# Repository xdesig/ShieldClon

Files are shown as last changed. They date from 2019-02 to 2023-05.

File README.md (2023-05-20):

# ShieldClon V 0.00 and 0.01 

## initial versions.

SlieldClon is a board designed, specifically for mClon. It allows secure connections to manipulate the robot. It has the basic components for its operation, as well as access to all free connections to be able to add new elements. The robot with ShieldClon feeds through a 18650 Li-ion battery 3.7V, which you can recharge through the board.
This plate can be complicated to weld by students that do not have much experience, since it has many components and pins very together, but it is a good challenge to learn.
From the mClon team, we consider it important that students understand the robot's internal functioning, who knows their components and what their function is, so we recommend starting from 4th of ESO not to give the plate already welded, unless previously practiced with protoShield. However, shieldClon can be a good option for work with younger students, always inviting them to connect the sensors and actresses on the shield pins themselves.
Is valid to be able to carry out many STEM projects based on Arduino

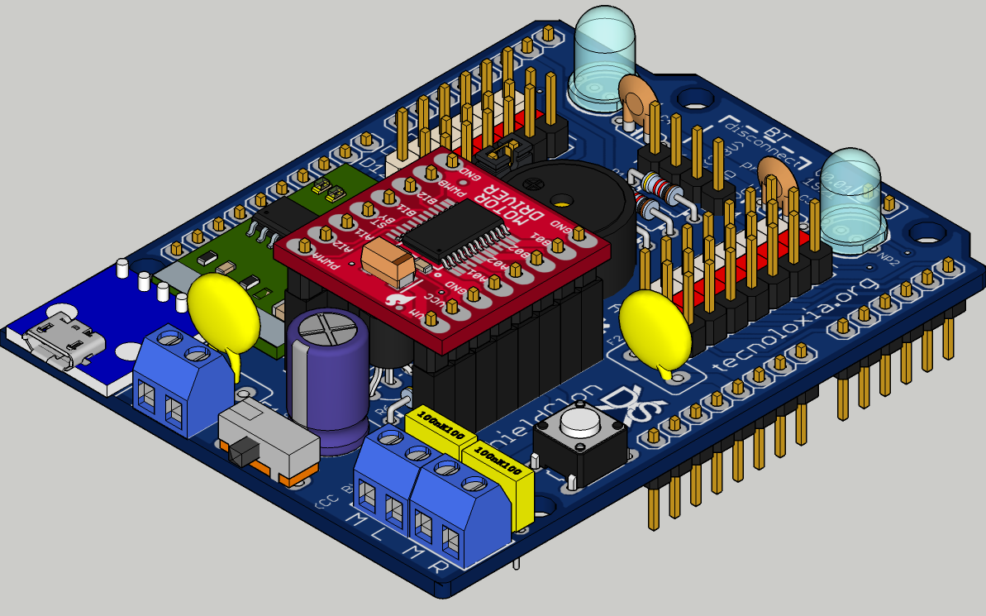
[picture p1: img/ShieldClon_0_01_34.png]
RENDER


### [Assembly manual][Man]
#### Deseñado en Estrimia con agarimo.

## Author and license
* Author: [XDeSIG][TWI01]
* License:
  CERN Open Hardware Licence Version 2 - Weakly Reciprocal"CERN-OHL-W"
  Doc. Attribution-ShareAlike 4.0 International "CCBY-SA4.0"
 

## More info:
[tecnoloxia.org]
## To buy boards

Developer don't produce boards to sell. Under [_provider_][provider]
directory there are instructions to order yourself.

<!-- links -->
[tecnoloxia.org]: https://tecnoloxia.org/mclon/que-e-mclon/
[CCBY-SA4.0]: http://creativecommons.org/licenses/by-sa/4.0/
[TWI01]: https://twitter.com/xdesig
[RENDER]: https://github.com/xdesig/ShieldClon/blob/master/img/ShieldClon_0_01_34.png
[provider]: https://www.pcbway.com/project/shareproject/W50475ASJ144_NanoClon_001_gerber_f511f448.html
[Man]: https://github.com/xdesig/ShieldClon/blob/master/ShieldClon_0_00/Montaxe_ShielClon.pdf

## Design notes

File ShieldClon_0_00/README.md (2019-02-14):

# ShieldClon V 0.00

## initial version.
Accessible connectors for basic function of MC LON. 
charge and discharge control for 3.7v batteries. 
Step-up voltage to 5V
Support for control of two engines in H bridge TB6612FNG.
Connection for two neopixel WS2812B through hole technology.
more info [tecnoloxia.org]
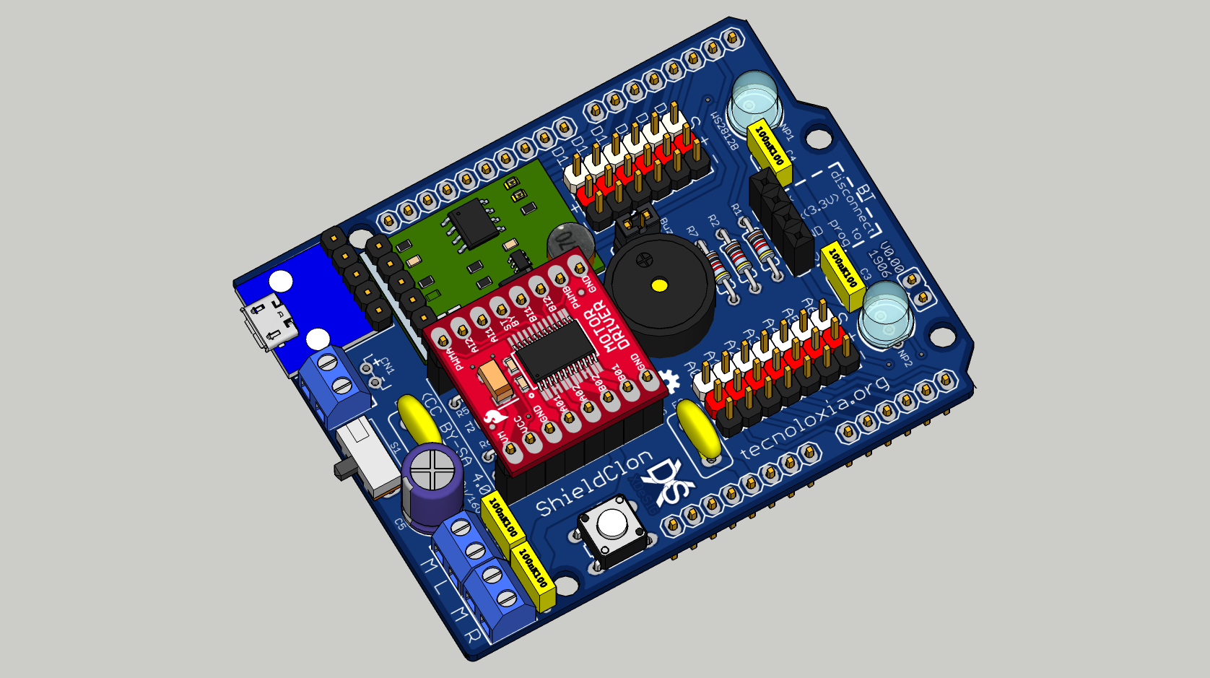
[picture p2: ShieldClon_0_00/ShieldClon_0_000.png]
Render ShieldClon 0.00


## Author and license
* Author: [XDeSIG][TWI01]
* License: [Attribution-ShareAlike 4.0 International] [CCBY-SA4.0]

<!-- links -->
[tecnoloxia.org]: https://tecnoloxia.org/mclon/que-e-mclon/
[CCBY-SA4.0]: http://creativecommons.org/licenses/by-sa/4.0/
[TWI01]: https://twitter.com/xdesig
[RENDER]: ShieldClon_0_000.png

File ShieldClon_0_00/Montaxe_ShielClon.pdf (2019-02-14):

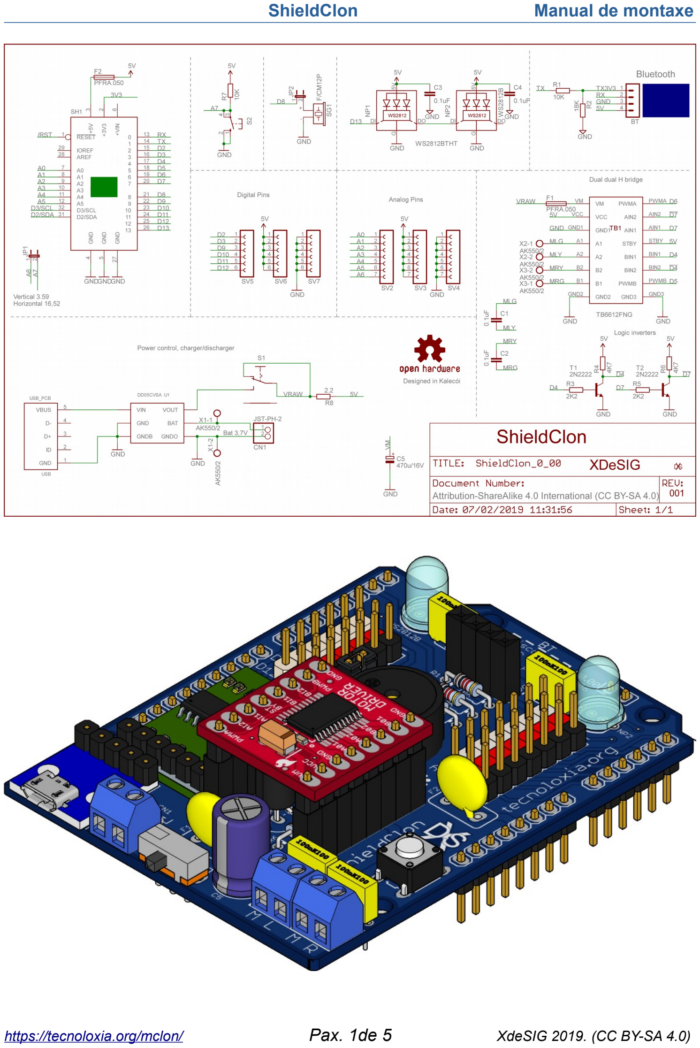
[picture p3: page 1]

ShieldClon | Manual de montaxe
https://tecnoloxia.org/mclon/ | Pax. 1de 5 | XdeSIG 2019. (CC BY-SA 4.0)

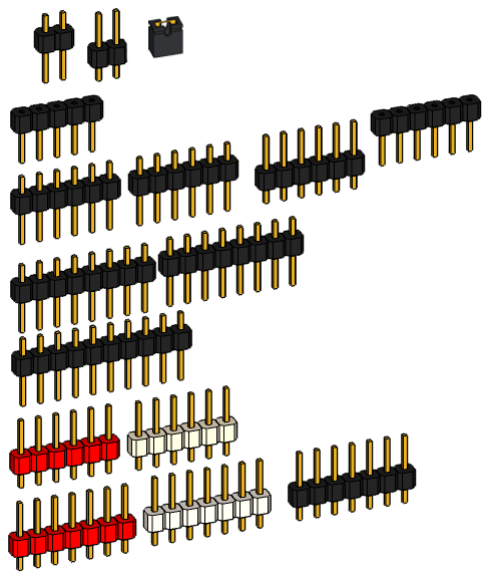
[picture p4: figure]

- Inventario de compoñentes.
- Tiras de postes
- 2 x 2 x 2,54mm + ponte
- 1 x 5 x 2,54mm
- 4 x 6 x 2,54mm
- 2 x 8 x 2,54mm
- 1 x 10 x 2,54mm
- 1 x 6 x 2,54mm Vermella
- 1 x 6 x 2,54mm Branca
- 1 x 7 x 2,54mm Vermella
- 1 x 7 x 2,54mm Branca
- 1 x 7 x 2,54mm Negra

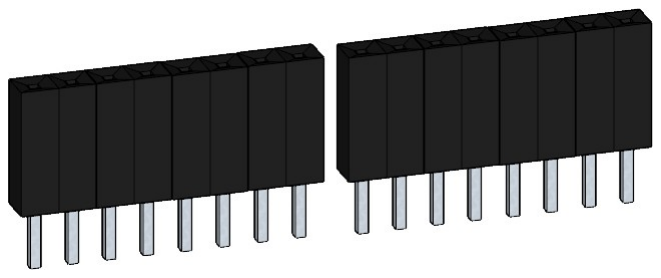
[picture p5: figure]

- Tiras Femia
- 1 x 4 x 2,54mm
- 2 x 8 x 2,54mm
- Bloques terminais
- 3 x 2 x 3,5mm
- Interruptor SK-12D07 e pulsador 6*6 6mm
- Resistencias:
- 2,2W, 18KW, 2 x 2K2W, 2 x 4K7W, 2 x 10KW.
- Condensadores:
- 4 x 100nF/≥16V, 470µF/≥16V
- Fusibles:
- 2 x Polyfuse 0,5mA
◦
- 2x LEDes NeoPixel WS2812B 5mm

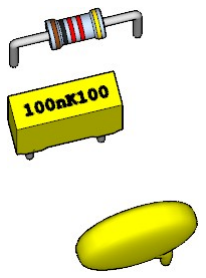
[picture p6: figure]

https://tecnoloxia.org/mclon/ | Pax. 2de 5 | XdeSIG 2019. (CC BY-SA 4.0)

- Módulos:
- Micro USB pcb
- Cargador/Booster
- Ponte “H” Dual

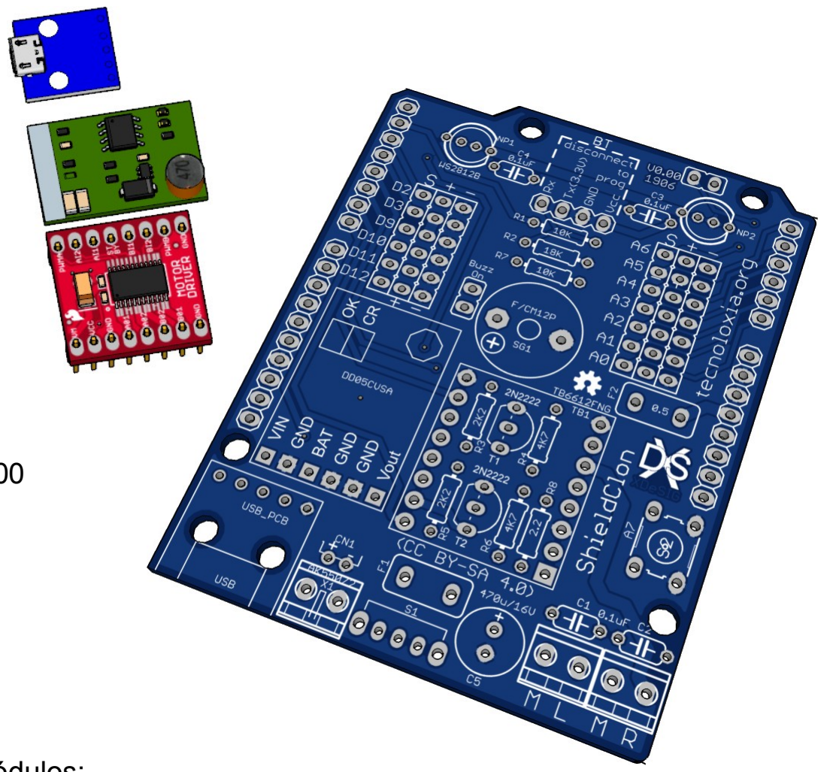
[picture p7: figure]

- PCB ShielClon V0,00
- Preparación dos módulos:
- Na placa micro USB tes que preparar unha tira de pins e baixalos de tal forma que queden cara abaixo, sóldao no modulo pola parte inferior,quedando como
na imaxe.

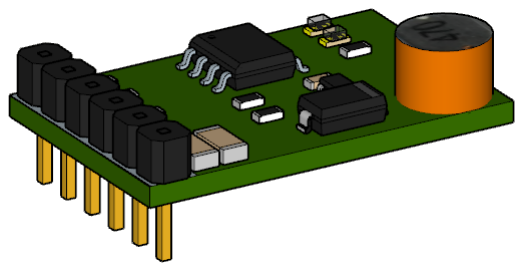
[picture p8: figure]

- No Cargador/Booster DD05CVSA fai o mesmo que na placa USB.
- A ponte “H” Dual TB6612FNG, xa
vén cos seus pines. Colócalos na parte inferior, procurando que queden o máis perpendiculares posible, sóldaos pola parte superior. Podes axudarte dunha protoboard
para pinchar os pins para que
queden perpendiculares (coidado ca

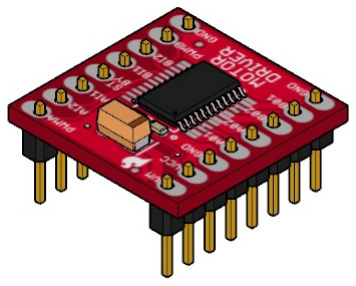
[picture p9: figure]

temperatura que protoboard non aguanta moito).

https://tecnoloxia.org/mclon/ | Pax. 3de 5 | XdeSIG 2019. (CC BY-SA 4.0)

- Na montaxe da placa, comeza polos compoñentes de baixo perfil, as resistencias. A placa ven serigrafiada cos

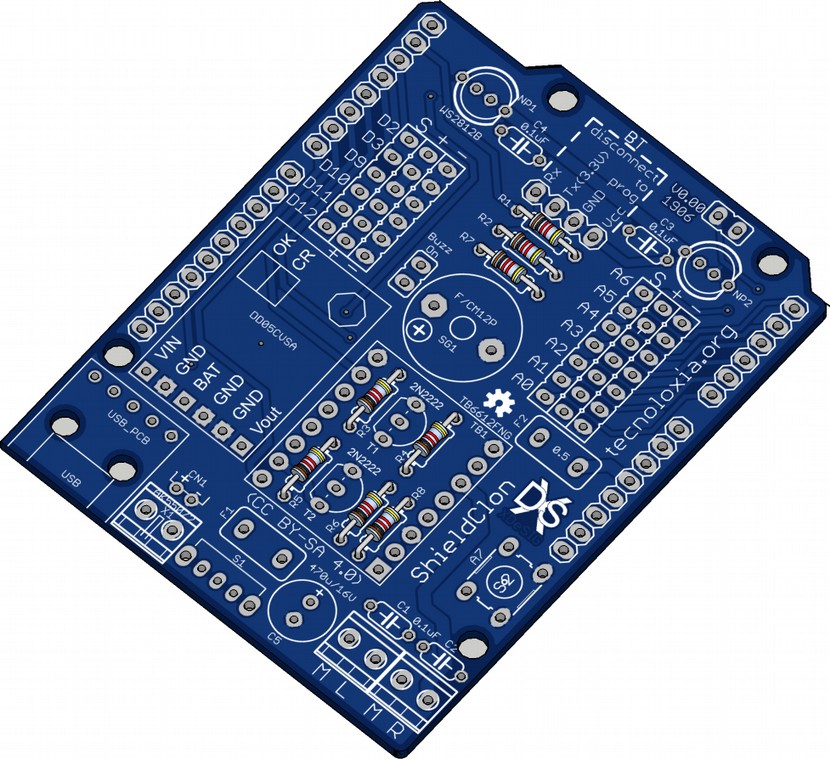
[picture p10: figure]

valores dos compoñentes. Vai soldando unha a
unha as resistencias, orientadas de tal forma
que sexan fáciles de ler, deixando a banda de tolerancia na dereita e vai cortando o sobrante das patas cada vez que soldes unha resistencia.
- Pasa a soldar os módulos que preparaches antes o modulo cargador/booster, e o adaptador USB ( podemos amarralo cunha brida que pasará polos buratos)

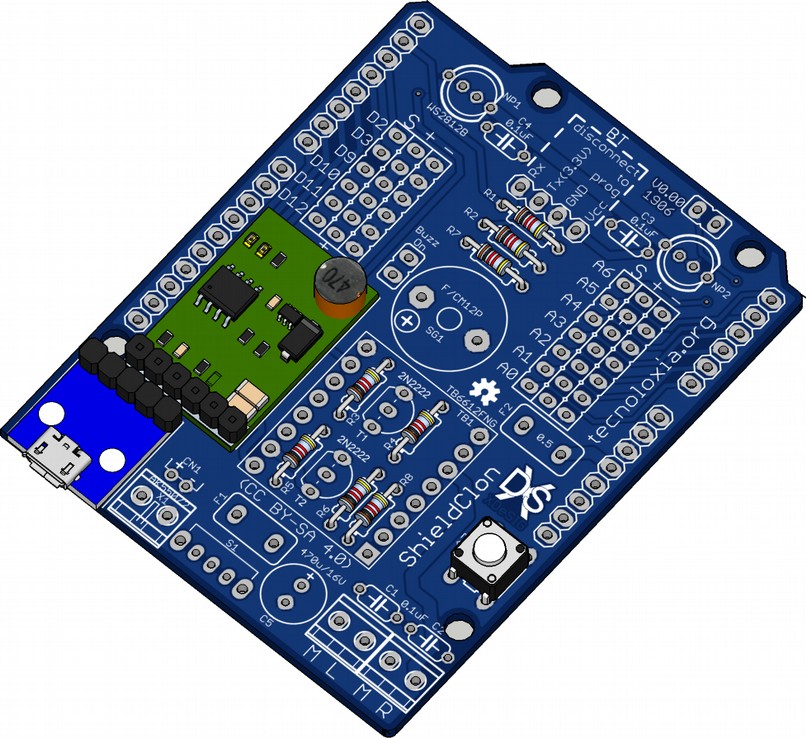
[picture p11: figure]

- Agora solda o interruptor, os conectores para os motores e alimentación.
Opcionalmente, se tes unha batería co conector JST-PH-2, podes soldar o conector macho nos Buratos CN1,
- Seguidamente soldamos os condensadores, os polyfuses e os transistores. Con estes últimos ten coidado de inserilos como se indica na serigrafía. Tamén ten coidado ao soldalos, pois só aguantan 300ºC durante 10 segundos.
- (Consello: solda unha pata de un transistor, e mentas soldas a do outro este se arrefria un pouco.)

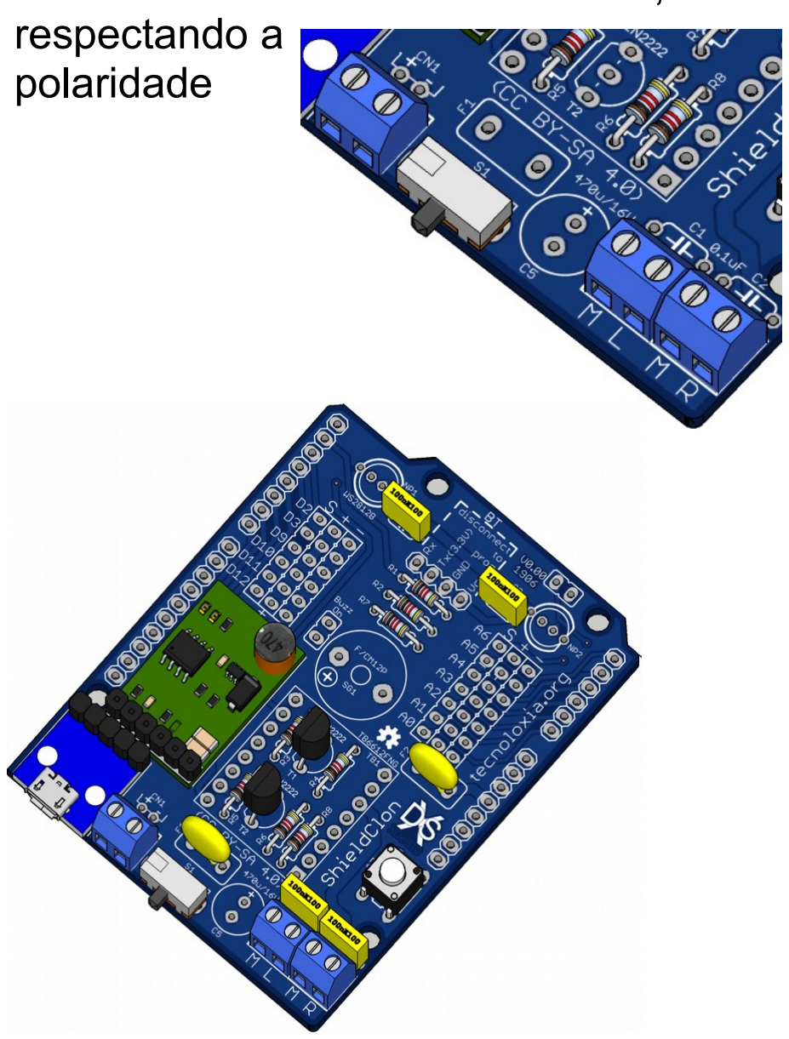
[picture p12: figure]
respectando a polaridade

https://tecnoloxia.org/mclon/ | Pax. 4de 5 | XdeSIG 2019. (CC BY-SA 4.0)

(ollo as cores das resistencias na imaxe non son correctas ) ☹

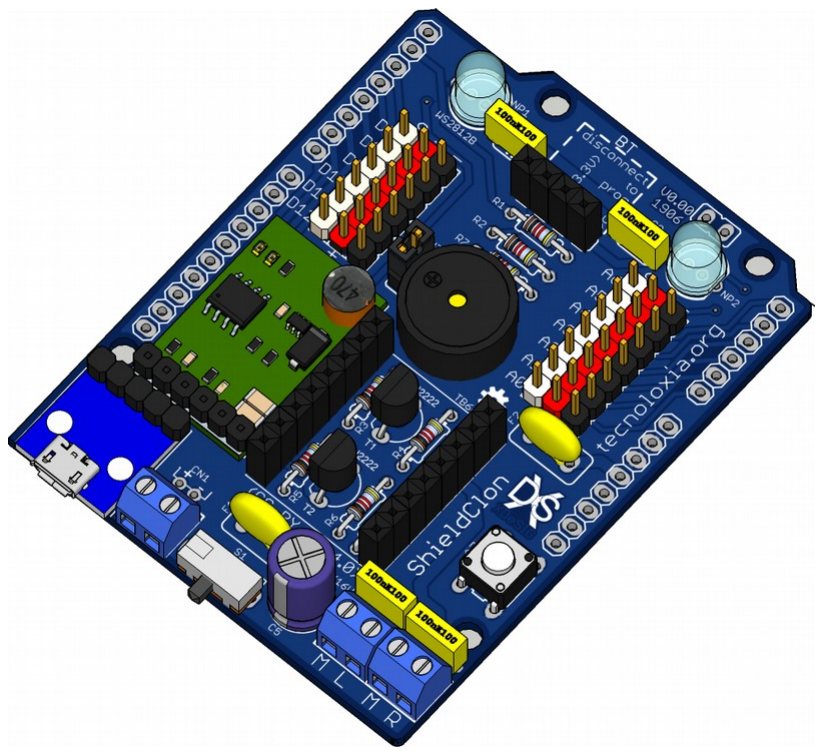
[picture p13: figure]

- Toca o momento de soldar os condensadores, LEDes, buzzer (comproba a serigrafía para unha correcta conexión), postes e as tiras femia para a ponte H dual e o Bluetooth. Podemos por postes con diferentes cores para deixar máis claras as conexións dos sensores e actuadores.
- Lembra ter coidado de queden o máis perpendiculares posible. Podes axudarte de outras tiras e postes para mantelos no sitio

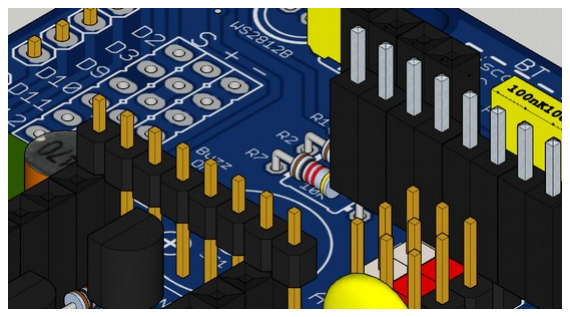
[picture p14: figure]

- Xa só resta soldar os postes na parte inferior e, como no paso anterior ten coidado de que queden o máis verticais posible. Podemos usar o mesmo truco de antes, ou pinchamos na placa do Arduino, para que sexa ela a que manteña verticais os postes.
- (non lle apliques moito calor pois os plásticos
non aguantan moito).
- Pincha o módulo da ponte H dual
- Xa tes a shieldClon montada, realiza unha

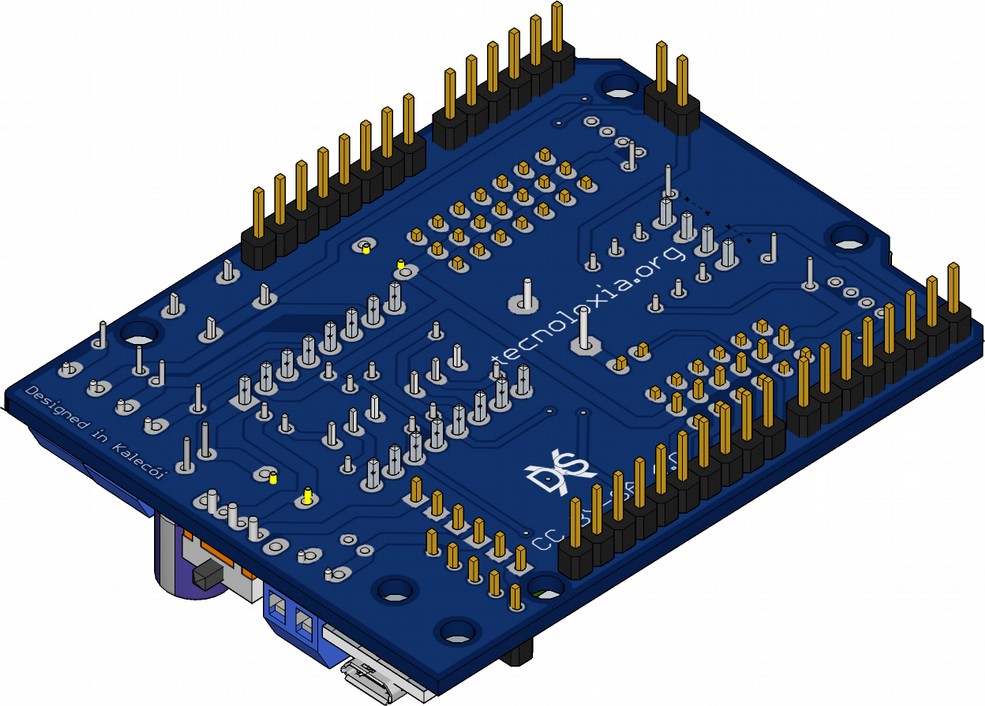
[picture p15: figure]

comprobación visual das soldaduras e que non quedou ningunha ponte que poida producir un curto circuíto.

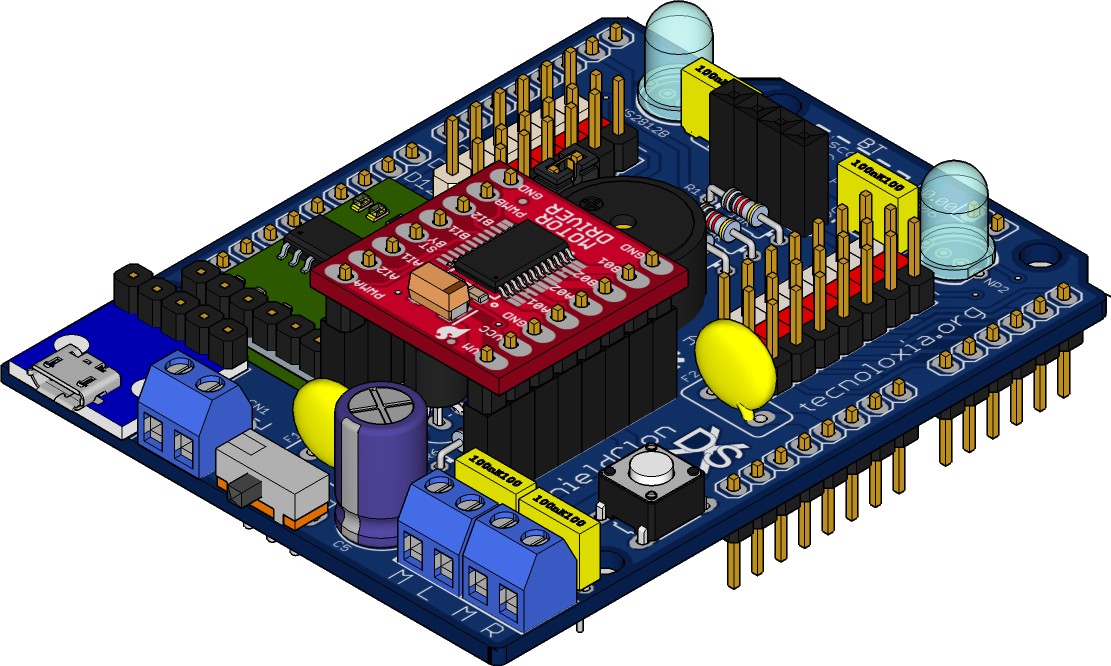
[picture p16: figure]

https://tecnoloxia.org/mclon/ | Pax. 5de 5 | XdeSIG 2019. (CC BY-SA 4.0)

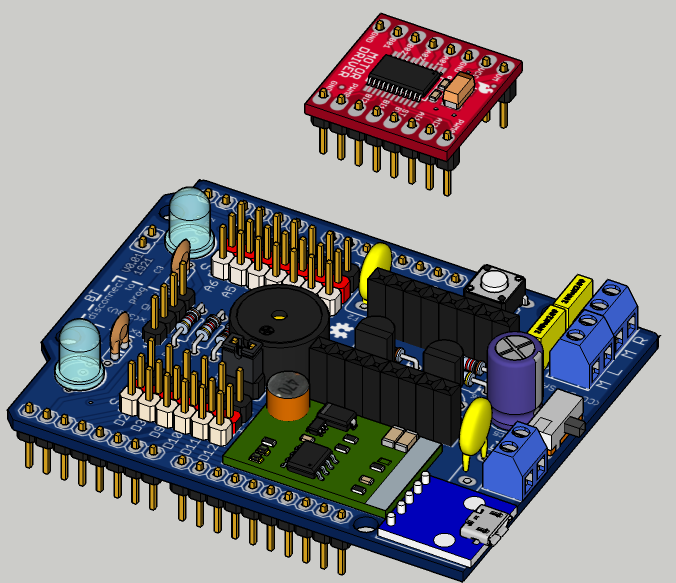
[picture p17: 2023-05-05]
ShieldClon_0_01/ShieldClon_0_01_43_.png

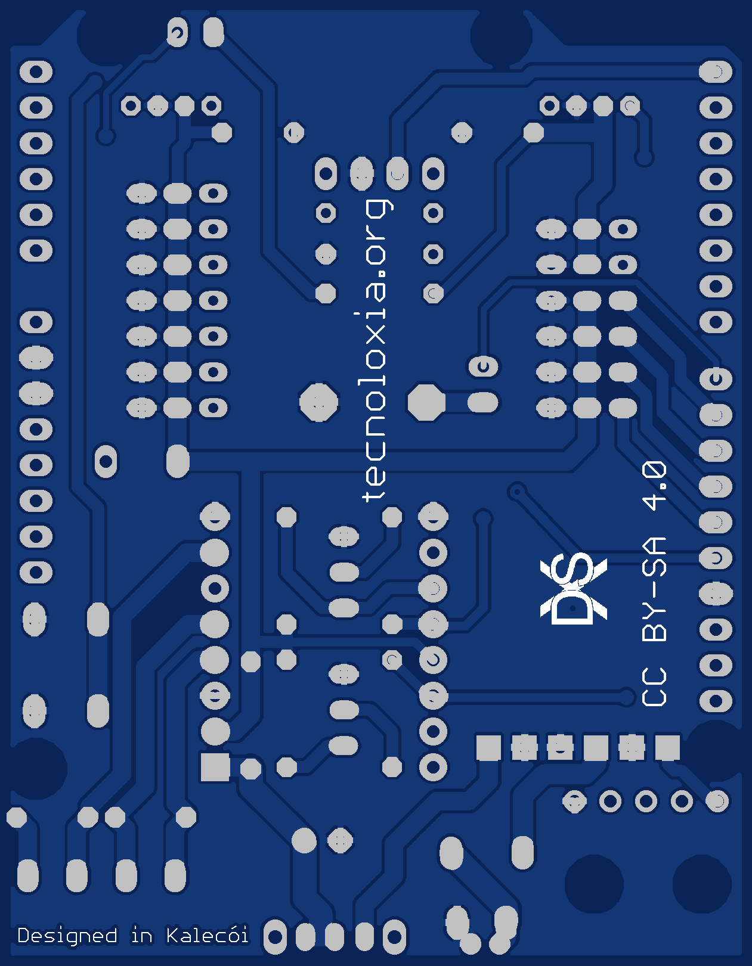
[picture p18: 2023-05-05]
ShieldClon_0_01/eagleUp_ShieldClon_0_01_board_bottom.png

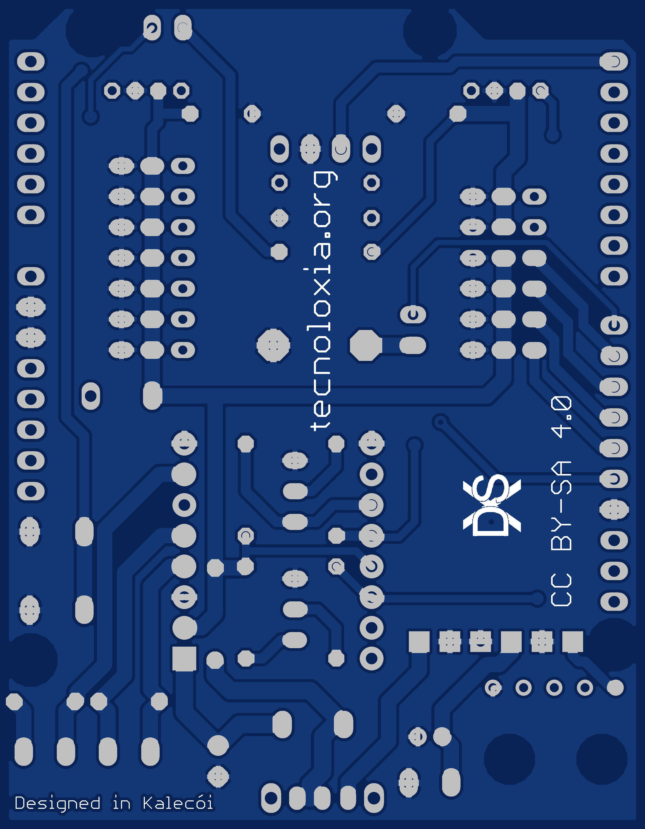
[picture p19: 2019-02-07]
ShieldClon_0_00/ShieldClon_0_00_board_bottom.png

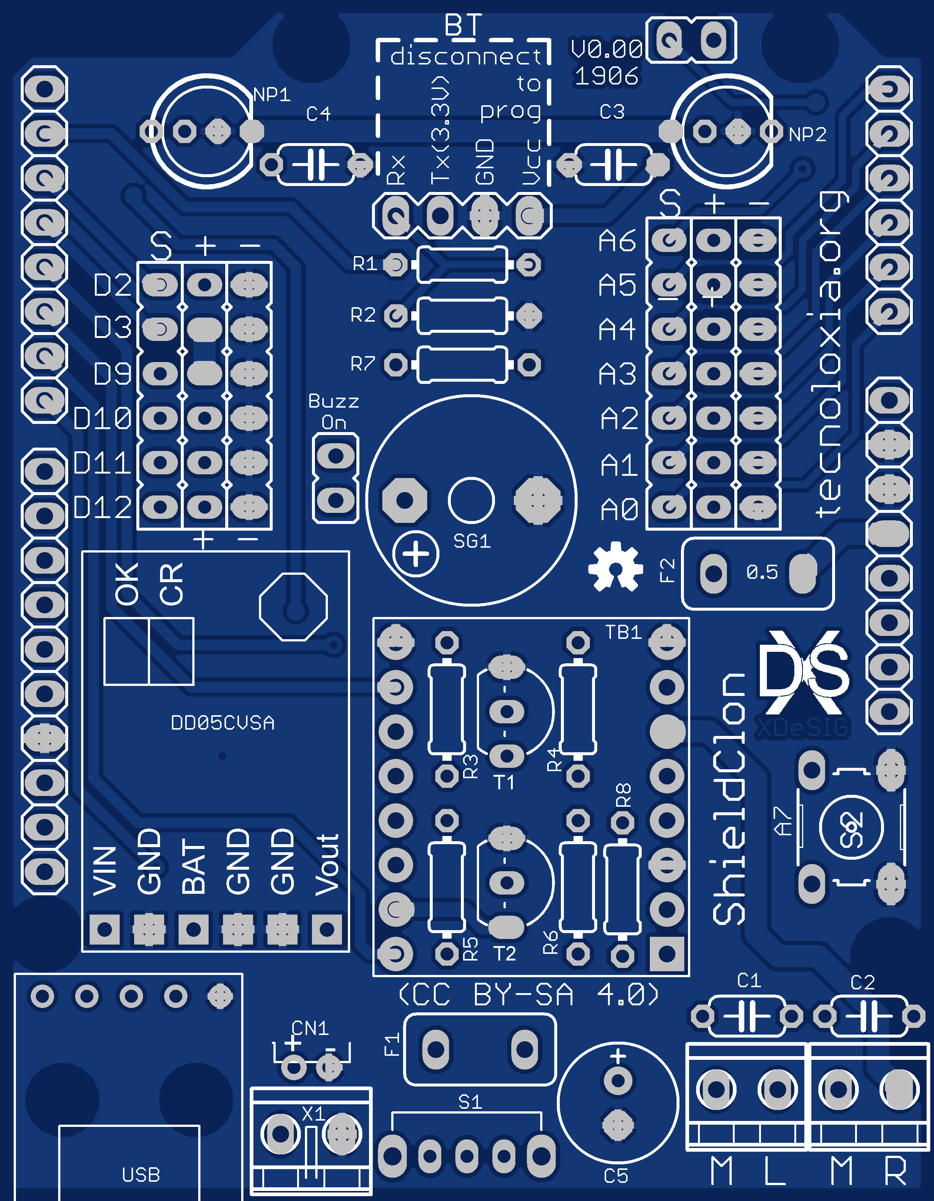
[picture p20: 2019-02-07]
ShieldClon_0_00/ShieldClon_0_00_board_top.png

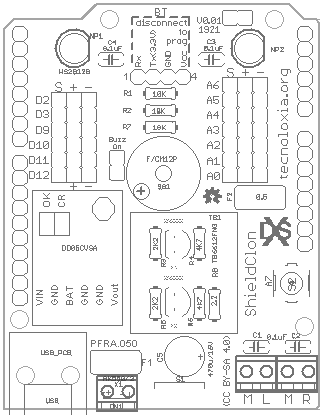
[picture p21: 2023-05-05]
ShieldClon_0_01/ShieldClon_0_01_SilkT.png

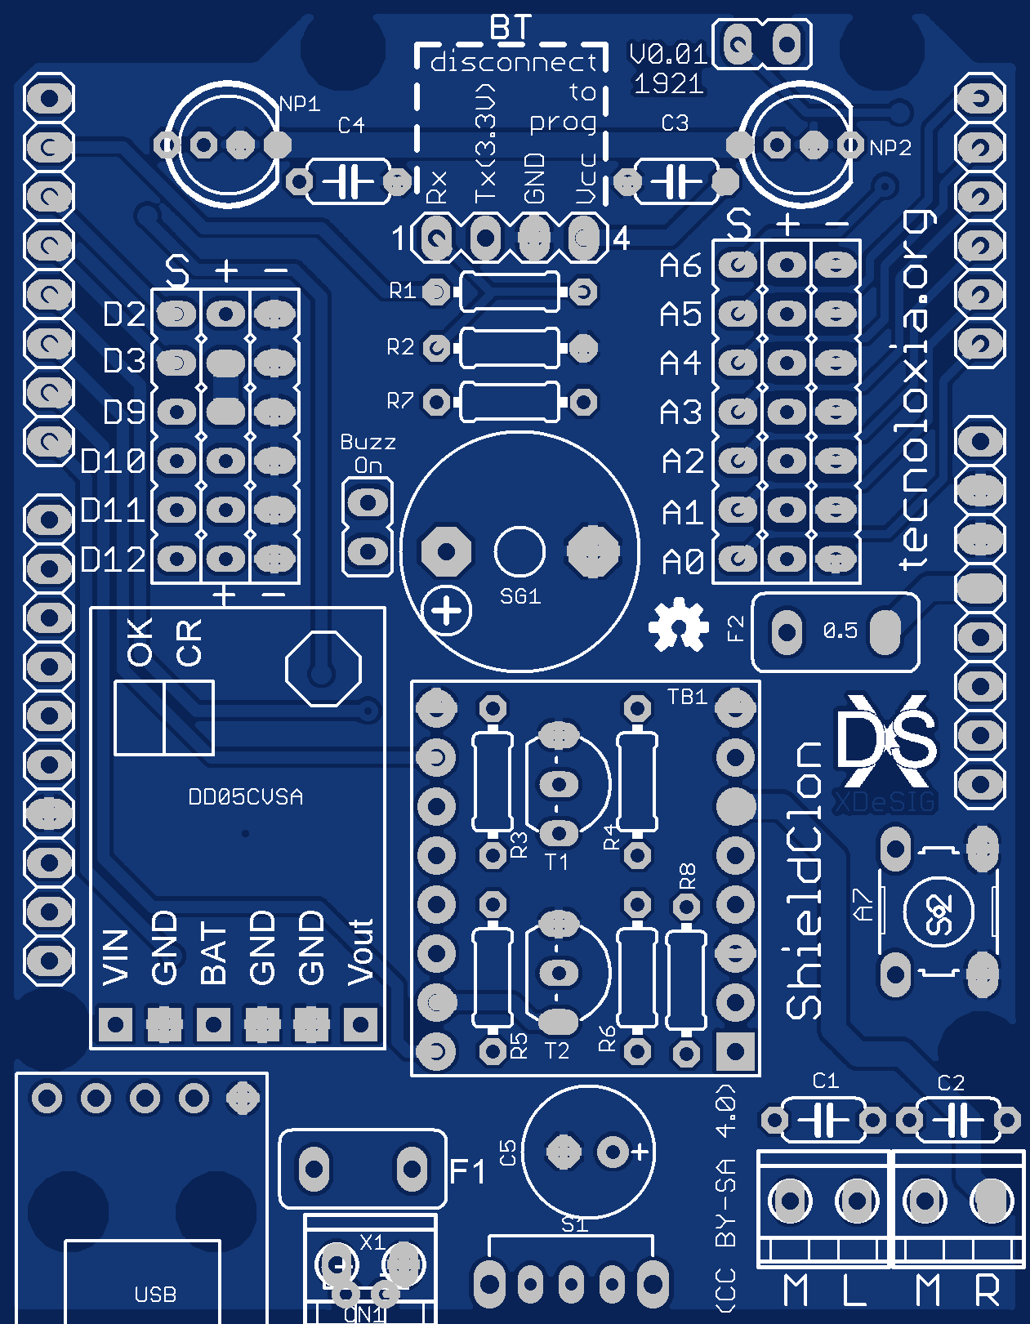
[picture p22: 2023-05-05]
ShieldClon_0_01/eagleUp_ShieldClon_0_01_board_top.png

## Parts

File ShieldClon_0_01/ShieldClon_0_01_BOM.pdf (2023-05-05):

Folla1

Páxina 1

ShieldClon 00-01
X DeSIG
Units | Value | Descr | Package | Pads | Parts | Sbt Pads | LCSC
1 | | White | 1x6Px2,54 | 6 SV5 | | 6 | C3329786 (https://www.lcsc.com/product-detail/Pin-Headers_MOLEX-0022032131_C3329786.html)
1 | | Red | 1x6Px2,54 | 6 SV6 | | 6 | C141437 (https://www.lcsc.com/product-detail/Pin-Headers_Ckmtw-Shenzhen-Cankemeng-S108500006_C141437.html)
1 | | Black | 1x6Px2,54 | 6 SV7 | | 6 | C2337 (https://www.lcsc.com/product-detail/Pin-Headers_BOOMELE-Boom-Precision-Elec-C2337_C2337.html)
1 | | White | 1x7Px2,54 | 7 SV2 | | 7 | C3329786 (https://www.lcsc.com/product-detail/Pin-Headers_MOLEX-0022032131_C3329786.html)
1 | | Red | 1x7Px2,54 | 7 SV3 | | 7 | C141437 (https://www.lcsc.com/product-detail/Pin-Headers_Ckmtw-Shenzhen-Cankemeng-S108500006_C141437.html)
1 | | Black | 1x7Px2,54 | 7 SV4 | | 7 | C2337 (https://www.lcsc.com/product-detail/Pin-Headers_BOOMELE-Boom-Precision-Elec-C2337_C2337.html)
1 | | With cap | 1x2Px2,54 | 2 JP2 | | 2 C376075
1 | | JUMPER_JP1E | 1x2Px2,54 Female | 2 JP1 | | 2 | C49661 (https://www.lcsc.com/product-detail/Female-Headers_BOOMELE-Boom-Precision-Elec-C49661_C49661.html)
1 | | MA04-1 | 1x4Px2,54 Female | 4 BT | | 4 | C2718488 (https://www.lcsc.com/product-detail/Female-Headers_BOOMELE-Boom-Precision-Elec-C2718488_C2718488.html)
4 0.1uF | | C-EU025-024X044 | C025-024X044 | 2 C1,, C4 | | 8 | C353903 (https://www.lcsc.com/product-detail/Ceramic-Disc-Capacitors_Dersonic-CC1H104ZA1PD3F5P3003_C353903.html)
2 10K | | R-EU_0204/7 | 0204/7 | 2 R1, R7 | | 4 | C61299 (https://www.lcsc.com/product-detail/Through-Hole-Resistors_UNI-ROYAL-Uniroyal-Elec-CFR0W4J0103A50_C61299.html)
1 18K | | R-EU_0204/7 | 0204/7 | 2 R2 | | 2 | C70811 (https://www.lcsc.com/product-detail/Through-Hole-Resistors_UNI-ROYAL-Uniroyal-Elec-CFR0W4J0183A50_C70811.html)
1 2.2 | | R-EU_0204/7 | 0204/7 | 2 R8 | | 2 | C2894548 (https://www.lcsc.com/product-detail/Through-Hole-Resistors_VO-CR1-4W-2-2-5-OT26_C2894548.html)
2 2K2 | | R-EU_0204/7 | 0204/7 | 2 R3, R5 | | 4 | C120063 (https://www.lcsc.com/product-detail/Through-Hole-Resistors_CCO-Chian-Chia-Elec-CF1-4W-2-2K-5-T_C120063.html)
2 4K7 | | R-EU_0204/7 | 0204/7 | 2 R4, R6 | | 4 | C120071 (https://www.lcsc.com/product-detail/Through-Hole-Resistors_CCO-Chian-Chia-Elec-CF1-4W-4-7K-5-T_C120071.html)
2 2N2222 | | 2N2222 | TO92-EBC-OVAL | 3 T1, T2 | | 6 | C5330385 (https://www.lcsc.com/product-detail/Bipolar-Transistors-BJT_Slkor-SLKORMICRO-Elec-2N2222A_C5330385.html)
1 470u/16V | | 470uF 16V | E2,5-7 | 2 C5 | | 2 | C2842806 (https://www.lcsc.com/product-detail/Aluminum-Electrolytic-Capacitors-Leaded_SamYoung-Electronics-NXA-16V-470UF-10-12-5-5-0TP_C2842806.html)
3 AK550/2 | | AK550/2 | AK550/2 3,5mm | 2 X1, X2, X3 | | 6 | C784940 (https://www.lcsc.com/product-detail/Screw-terminal_Ningbo-Xinlaiya-Elec-XY302V-3-5-2P_C784940.html)
1 F/CM12P | | BUZZER 12mm (7mm) | F/CM12P | 2 SG1 | | 2 | C2689171 (https://www.lcsc.com/product-detail/Buzzers_S-S-SUN-1295Y-0327-45P7-6_C2689171.html)
2 PFRA.050 | | Polyfuse 0.65A | TE5 | 2 F1, F2 | | 4 | C1562414 (https://www.lcsc.com/product-detail/Resettable-Fuses_SCHURTER-PFRA-050_C1562414.html)
1 TB6612FNG | | TB6612FNG on PCB | TB6612FNG | 16 TB1 | | 16
1 USB_PCB | | Micro USB | MicroXNJ | 4 USB | | 4 | C404969 (https://www.lcsc.com/product-detail/span-style-background-color-ff0-USB-span-Connectors_SHOU-HAN-MicroXNJ_C404969.html)
2 WS2812B | | WS2812BTHT | NEOPIXEL5MM | 4 NP2 | | 8 | C114586 (https://www.lcsc.com/product-detail/Light-Emitting-Diodes-LED_Worldsemi-WS2812B-B-W_C114586.html)

Charger/step up option
1 DD05CVSA | DD05CVSA | DD05CVSA | 6 U1 | 6
| | | Total PADS | 125

Aliexpress (https://es.aliexpress.com/item/32223093678.html)

https://es.aliexpress.com/i/32828274599.html

Folla1

Páxina 2

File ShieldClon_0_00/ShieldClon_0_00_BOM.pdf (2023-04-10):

Folla1

Páxina 1

ShieldClon 00-01 | XdeSIG
Units | Value | Descr | Package | Parts | LCSC
1 | | White | 1x6Px2,54 | SV5 | C3329786 (https://www.lcsc.com/product-detail/Pin-Headers_MOLEX-0022032131_C3329786.html)
1 | | Red | 1x6Px2,54 | SV6 | C141437 (https://www.lcsc.com/product-detail/Pin-Headers_Ckmtw-Shenzhen-Cankemeng-S108500006_C141437.html)
1 | | Black | 1x6Px2,54 | SV7 | C2337 (https://www.lcsc.com/product-detail/Pin-Headers_BOOMELE-Boom-Precision-Elec-C2337_C2337.html)
1 | | White | 1x7Px2,54 | SV2 | C3329786 (https://www.lcsc.com/product-detail/Pin-Headers_MOLEX-0022032131_C3329786.html)
1 | | Red | 1x7Px2,54 | SV3 | C141437 (https://www.lcsc.com/product-detail/Pin-Headers_Ckmtw-Shenzhen-Cankemeng-S108500006_C141437.html)
1 | | Black | 1x7Px2,54 | SV4 | C2337 (https://www.lcsc.com/product-detail/Pin-Headers_BOOMELE-Boom-Precision-Elec-C2337_C2337.html)
2 | | + 1 cap | 1x2Px2,54 | JP1,JP2 | C376075
1 | | MA04-1 | 1x4Px2,54 Female | BT | C2718488 (https://www.lcsc.com/product-detail/Female-Headers_BOOMELE-Boom-Precision-Elec-C2718488_C2718488.html)
4 0.1uF | | C-EU025-024X044 | C025-024X044 | C1,, C4 | C353903 (https://www.lcsc.com/product-detail/Ceramic-Disc-Capacitors_Dersonic-CC1H104ZA1PD3F5P3003_C353903.html)
2 10K | | R-EU_0204/7 | 0204/7 | R1, R7 | C61299 (https://www.lcsc.com/product-detail/Through-Hole-Resistors_UNI-ROYAL-Uniroyal-Elec-CFR0W4J0103A50_C61299.html)
1 18K | | R-EU_0204/7 | 0204/7 | R2 | C70811 (https://www.lcsc.com/product-detail/Through-Hole-Resistors_UNI-ROYAL-Uniroyal-Elec-CFR0W4J0183A50_C70811.html)
1 2.2 | | R-EU_0204/7 | 0204/7 | R8 | C2894548 (https://www.lcsc.com/product-detail/Through-Hole-Resistors_VO-CR1-4W-2-2-5-OT26_C2894548.html)
2 2K2 | | R-EU_0204/7 | 0204/7 | R3, R5 | C120063 (https://www.lcsc.com/product-detail/Through-Hole-Resistors_CCO-Chian-Chia-Elec-CF1-4W-2-2K-5-T_C120063.html)
2 4K7 | | R-EU_0204/7 | 0204/7 | R4, R6 | C120071 (https://www.lcsc.com/product-detail/Through-Hole-Resistors_CCO-Chian-Chia-Elec-CF1-4W-4-7K-5-T_C120071.html)
2 2N2222 | | 2N2222 | TO92-EBC-OVAL | T1, T2 | C5330385 (https://www.lcsc.com/product-detail/Bipolar-Transistors-BJT_Slkor-SLKORMICRO-Elec-2N2222A_C5330385.html)
1 470u/16V | | 470uF 16V | E2,5-7 | C5 | C2960374 (https://www.lcsc.com/product-detail/Aluminum-Electrolytic-Capacitors-Leaded_HRK-10V470uF-CD288_C2960374.html)
3 AK550/2 | | AK550/2 | AK550/2 3,5mm | X1, X2, X3 | C784940 (https://www.lcsc.com/product-detail/Screw-terminal_Ningbo-Xinlaiya-Elec-XY302V-3-5-2P_C784940.html)
1 F/CM12P | | BUZZER 12mm (7mm) | F/CM12P | SG1 | C2689171 (https://www.lcsc.com/product-detail/Buzzers_S-S-SUN-1295Y-0327-45P7-6_C2689171.html)
2 PFRA.050 | | Polyfuse 0.65A | TE5 | F1, F2 | C1562414 (https://www.lcsc.com/product-detail/Resettable-Fuses_SCHURTER-PFRA-050_C1562414.html)
1 TB6612FNG | | TB6612FNG on PCB | TB6612FNG | TB1
1 USB_PCB | | Micro USB | MicroXNJ | USB
2 WS2812B | | WS2812BTHT | NEOPIXEL5MM | NP2

Charger/step up option
1 DD05CVSA | DD05CVSA | DD05CVSA | U1

Aliexpress
Aliexpress (https://es.aliexpress.com/item/32223093678.html)
sparkfun

aliexpress (https://es.aliexpress.com/i/32828274599.html)

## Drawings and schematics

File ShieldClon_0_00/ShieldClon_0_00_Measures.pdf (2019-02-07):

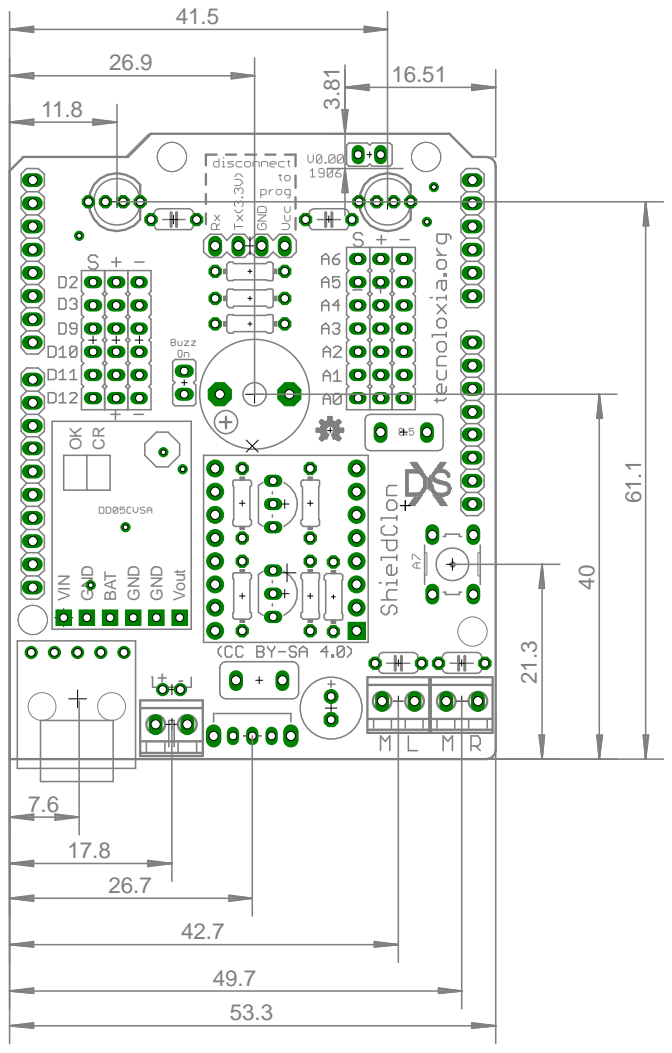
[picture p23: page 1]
VIN; GND; BAT; Vout

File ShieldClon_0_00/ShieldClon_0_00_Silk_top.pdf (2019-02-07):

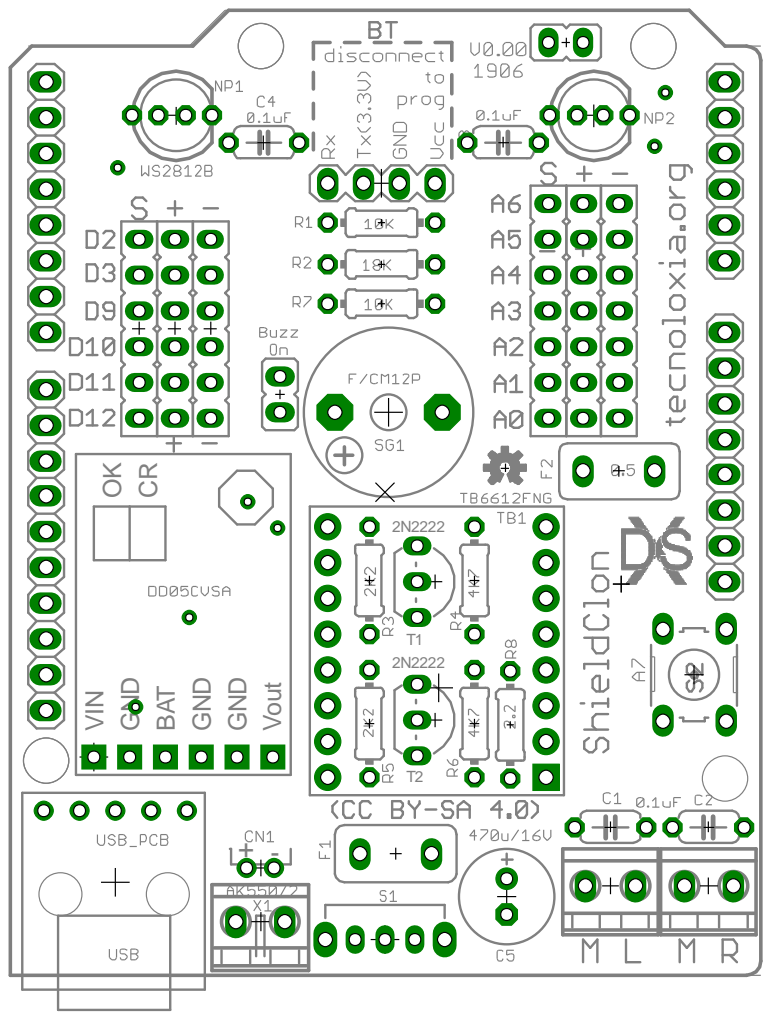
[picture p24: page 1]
VIN; GND; BAT; Vout

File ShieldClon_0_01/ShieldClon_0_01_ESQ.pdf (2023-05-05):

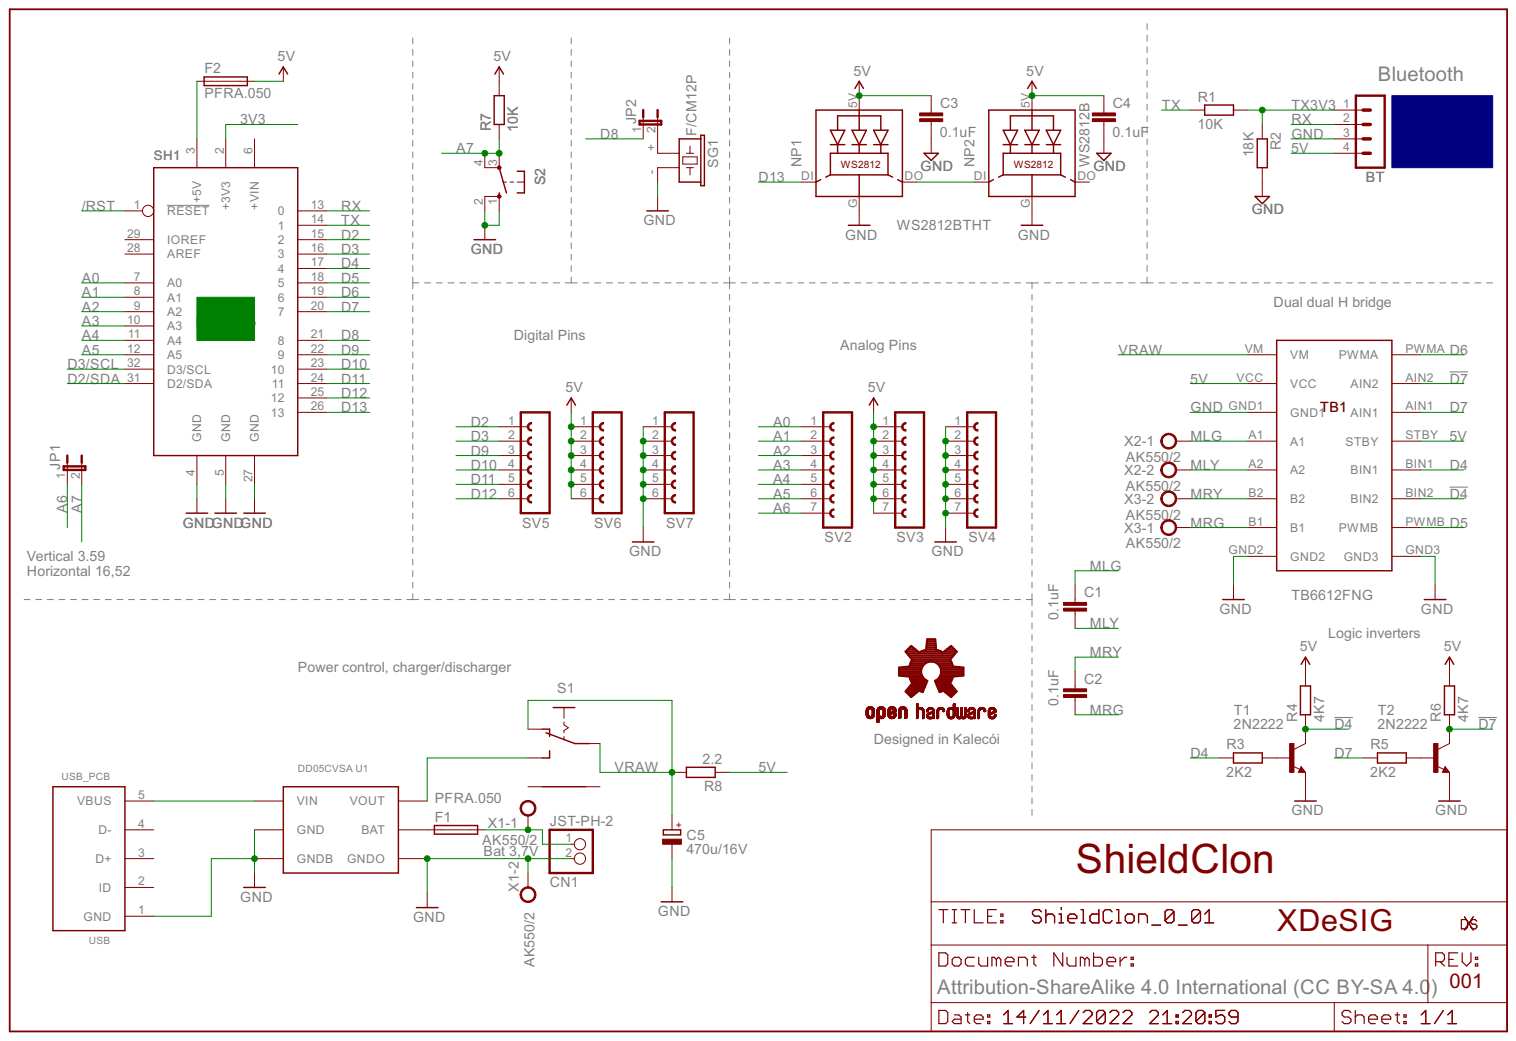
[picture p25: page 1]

Attribution-ShareAlike 4.0 International (CC BY-SA 4.0)

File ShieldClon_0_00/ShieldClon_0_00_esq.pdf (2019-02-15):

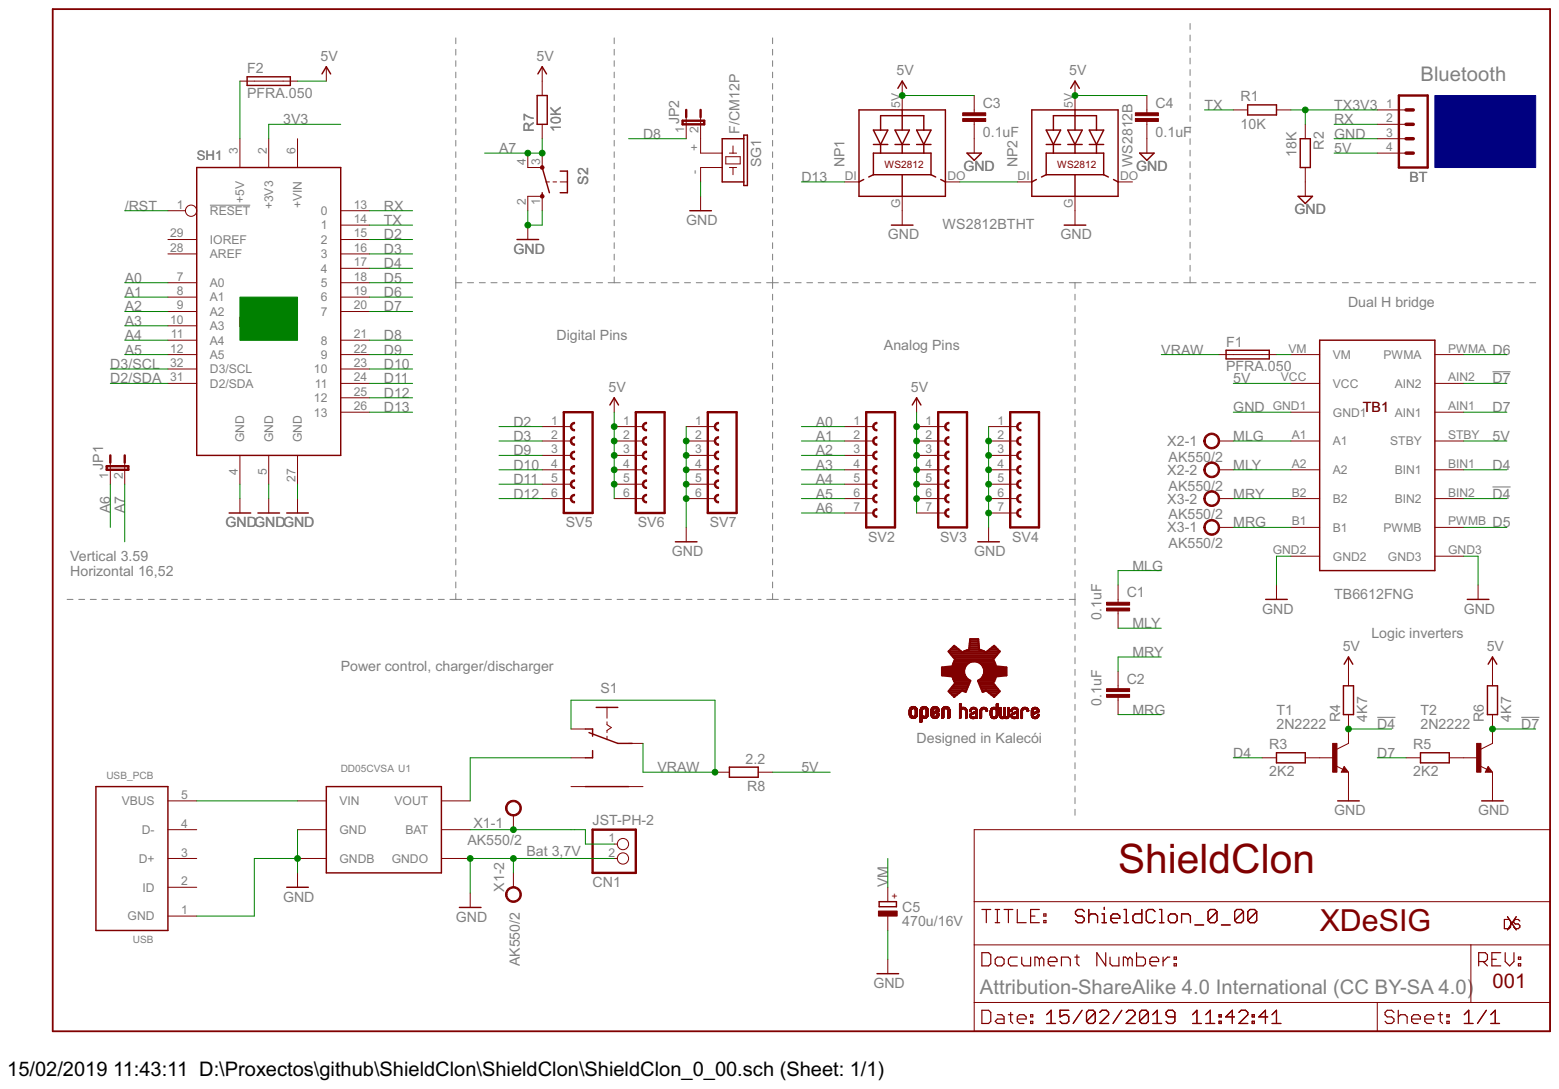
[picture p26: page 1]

Attribution-ShareAlike 4.0 International (CC BY-SA 4.0)

15/02/2019 11:43:11 D:\Proxectos\github\ShieldClon\ShieldClon\ShieldClon_0_00.sch (Sheet: 1/1)

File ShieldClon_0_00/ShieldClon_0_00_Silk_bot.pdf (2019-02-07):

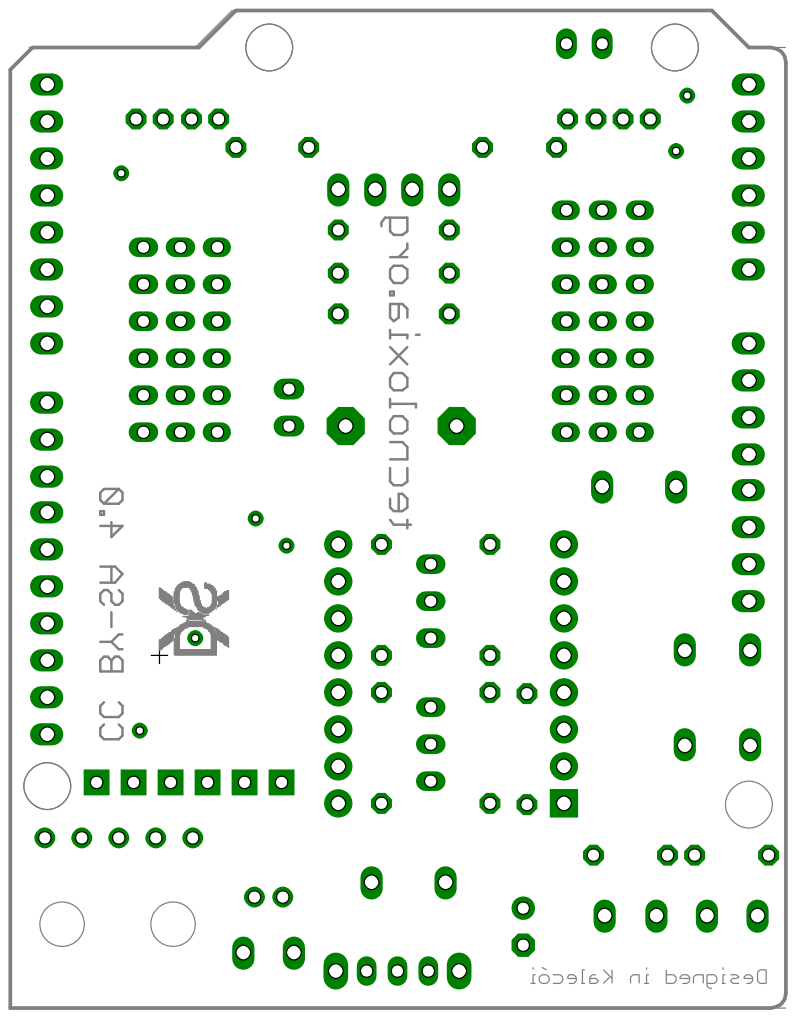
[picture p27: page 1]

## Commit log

2019-02-12 Bom added
    [ShieldClon_0_00.brd]
2019-02-14 add mount guide
2019-02-14 Add Assembly guide
2019-02-15 BOM ODS add
    [ShieldClon_0_00.sch, ShieldClon_0_00_BOM.ods]
2020-05-30 Add BOM .odt
    [ShieldClon_0_00_BOM.ods]
2023-03-13 Update BOM
    [ShieldClon_0_00_BOM.ods]
